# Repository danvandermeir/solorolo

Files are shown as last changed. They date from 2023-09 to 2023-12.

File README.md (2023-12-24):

# SoloRolo
  
This is a FOS(S) set of code and CAD files to assist in creating a single hub motor self balancing skateboard. As I said, this is provided for free. I take no responsibility for whatever may happen with creation of devices from these files. You are (at) your own risk. It is 3D printed, so how strong it is can depend heavily on what you print it with.  
  
That being said, riding around on this thing has been amazing and it has been a great time putting it together. Thanks for the interest. :)  
  
TL;DR for `original` SoloRolo:  
1. choose a battery size using notes at the bottom of this README  
2. choose if you want nice LED headlights (does not effect battery life worth talking about)
3. choose if you want underglow (RGB, can chase ground with rainbow)
4. choose LED strip types (individually addressable [RGB], RGB "analog")
5. download+print [these](mechanical/plastics/)  
6. order [these](BOMs/original/)  
7. check+cut [these](mechanical/metals/original/)  
8. assemble *everything* using [this](electrical/original/) and [this](finished/original/)  
9. program [ESC](code/ESCs/original/) and [Arduino](code/controllers/original/)  
10. button up and roll  
  
**In specific my recommend for creation of a SoloRolo is loosely this order, and it should be inferred that if a named collection does not have an entry in any subsection that `orignal` is to be used:**
1. Take note of the structure of files here so you know you're getting everything you need. It's actually easier done than said.
2. Read about and print/PIM/order [plastics](mechanical/plastics/) as they will take a "long time" to print, even if ordering from a 3D print or PIM company. This is the choice likely to have the most effect on look/feel and other part requirements. Start printing the electronics plate first if you have to make a choice, followed by the resistive footpad.
3. Start putting together and making orders for your parts based on the [original BOM](BOMs/original/). Preferably starting with your frame material from the next step so you can deliberate on certain details without delaying your whole project. If there are different requirements for your named collection they'll be found in [BOMs](BOMs/).
4. Start assembling your electronics. Take your time, and do a good job.
5. Read about and order/cut your [metals](mechanical/metals/). Check for a subsection for your chosen named collection (or use `original`), and start cutting.
6. Now that you have a metal frame to more reasonably mount and attach the hub motor and ESC parts to read about and program your [ESC](electronics/ESCs/). These can be expensive and should be the first thing to verify. Any differing files from the VESC based FESC will be under it's respective subsection.
7. LEDs! And... everything else. You'll need to wait for your electronics plate print. Run all your wires through your frames, stick all your LEDs on the frame that are going there, and mount your electronics to your electronics plate. This will allow easier access to everything as it's all coming together now! :D Absolutely consult the [electronics schematic](electronics/) for your named collection (or `original`).
8. Program your Arduino, lighting controller, or whatever your named collection specifies and test the lights. Usually you can test by mounting your frame to a milk carton and tilting it while applying pressure to to the resistive sensors to verify proper power connections, communication between the lighting controller and the ESC, and proper power and/or data between the lighting controller and the LEDs and or strips.
9. When all your prints are in, assemble all the things! Fasten your cavities to your frame after fishing your wires through during assembly, install all your external interfaces (charge inlet, power button, LEDs and/or strips, screens, readouts, etc), connect all the loose power and data wires according to the [electronics schematic](electronics/) for your named collection (or `original`), fasten your footpads to your cavities, and install any caps or friction coatings (skateboard tape).
10. Test all your functions using your milk crate mount or whatever you've devised, and take 'er out on a catious maiden voyage! Roll! You're probably done! :D  

## The `solorolo_` * `_` * `-`* files subsections, and notes:  
***The first wildcard represents the design name of the parts collection.***  
I designed and uploaded `original`. If I don't like a design change to my orignal designs you can make your own (even if you want to start with mine as a base!) and contribute it under new directory names for replacement/required files.

***The second wildcard represents a battery size.***  
While having a large battery can be a benefit there are a few drawbacks such as weight, length, and usable capacity. The `max` size battery is 48 volts with a ? Amp hour (~960 Watt hour) rating yielding loosely 50-60 miles (85-90 kilometers) per full charge.  
- The weight of the `max` size battery SoloRolo is ~37 pounds (~16.75 kilograms). Is it worth lugging this around?  
<sub>It is for me... I live in a relatively remote area, this is great for exploring where I am not likely to use my SoloRolo for bunny hoping between many indoor locations where I may be able to charge.</sub>
  
- With the `max` size battery at maybe 60 miles (90 kilometers) capacity per charge combined with loosely what is considered a reasonable safe top speed of 18 m/h (~30 km/h) you could potentially be riding for 3 hours and 20 minutes! Will you come close to using this capacity?  
<sub>While rolling is an excellent time, that is a decently long duration that you may never approach with chargers at your stops. Again, I live in a relatively remote area.</sub>
  
- The length of the `max` size battery will limit the terrain and/or incline you are trying to travel. Do you have any steep streets you're looking to roll on?  
<sub>For me there are many steep paved and unpaved paths I take, but even so I can often find a another way up/down.</sub>

***The third and final wildcard represents the name of the part in the size and collection.***

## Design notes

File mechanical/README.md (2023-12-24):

These are the CAD files to be used for 3D printing, PIM, and/or cutting/ordering metals.

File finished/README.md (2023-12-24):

A space for named collections to store some finished product photos, partially to help assembly. Probably mostly glamor shots.

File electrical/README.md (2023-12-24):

Named collections of electrical schematics for a SoloRolo.

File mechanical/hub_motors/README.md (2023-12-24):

Creator named collections of hub motors in case `orignal` isn't for you.  
  
Also, really, it is helpful if you model all your parts that you are creating CAD models to interface with.

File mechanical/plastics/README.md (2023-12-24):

Creator named collections of parts files for 3D printing or PIM to be printed/made/ordered.  
  
If printing yourself absolutely consider using stronger, weather resistant, and more heat resistant plastics for this project. PETG can generally withstand higher weights, sudden shock, and is more heat resistant than most PLA. 3D printing plastics can be complex. YMMV Don't strand yourself due to a structural issue on a roll. /helicopterparent  
  
Following [original](original/) settings of footpads/electronics plate @0.1mm height, 10 perimeter layers, and 100% infill the cavities with these settings took loosely 4 and 4.5 days of continous printing. The footpads took 3.5 and 4 days. The electronics plate under a day. Perhaps consider starting your prints first with the electronics plate followed by the resistive footpad.

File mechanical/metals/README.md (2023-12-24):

Creator named models and mechanical drawings of/for the frame of your SoloRolo.

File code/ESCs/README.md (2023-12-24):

These are named collections of configuration files and instructions for use of Electronic Speed Controllers. Such as the VESC based FESC ESCs.

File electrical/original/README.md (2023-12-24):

This is a loose schematic for the current headlight and underglow iteration I have chosen. Prper update coming soon.

Conceptually the schematic isn't terribly complex.
```
Charge Port > Battery
                v
          Anti Spark Switch > VESC > Hub Motor
                v              v v
 v----< Constant Voltage PSU   | >   Resistor Network
 |              v              |            v
 |      Constant Current PSU   |     Pressure Sensitive Resistors
 |              v              v
 |        Transistor Pair   <  Arduino Nano
 |              v              v
 |    "Custom" LED Headlights  v
 |                             v
 >---------------------------->WS2812B LED strips (bumper1, bumper2, ground)
```
Eventually I will add more variants.

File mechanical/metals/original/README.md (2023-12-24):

-o-

These are the original STL and drawing files I created for cutting aluminum extrusion. An enormous amount of care and detail went into these (measure 9 times, cut 2, print 20, or something). Obligitory "please communicate/contibute" if you see valid changes you'd like to make. :)

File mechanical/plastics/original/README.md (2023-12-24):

-o-

These are the original STL files I created for 3D printing. An enormous amount of care and detail went into these (measure 9 times, cut 2, print 20, or something). Obligitory "please communicate/contibute" if you see valid changes you'd like to make. :)
  
There are headlight cavity and headlight electronics plate models for use with the extra LED Cree headlights listed in the `original` BOM. The Cree LED headlights are optional, but IMO worth it.  
  
I tried following design rules that reduce required support material for 3D printing, and incorperating all holes into the plastic where possible. Cutting metal is more difficult than reprinting for iterative design changes.  
  
Absolutely consider using stronger, weather resistant, and more heat resistant plastics for this project. PETG can generally withstand higher weights, sudden shock, and is more heat resistant than most PLA. 3D printing plastics can be complex. YMMV Don't strand yourself due to a structural issue on a roll.  
  
I used an Elegoo Neptune 3 Max in a "weather sealed" closed, Octoprint on a RPi4B, and around 6 1 kilogram spools of 1.75 millimeter Overture transparent PETG. All prints that I performed were printed at 100% infill with 10 top, bottom, and vertical perimeter layers. My first layer was single layer height (0.1/0.3 millimeter), 40 millimeter brims, no skirt, and organic supports at 40 degrees. The footpads and electronics plate were printed at 0.1 millimeter layer height with the rest being printed at 0.3 millimeter layer height. I did have to watch the footpads print pretty closely as I was closer to the ocean at the time and had a lot of issues with blobing.  
  
The cavities with these settings took loosely 4 and 4.5 days of continous printing. The footpads took 3.5 and 4 days. The electronics plate under a day. Perhaps consider starting your prints first with the electronics plate followed by the resistive footpad.

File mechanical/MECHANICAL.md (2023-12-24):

These are the original STL files I created for 3D printing and cutting aluminum extrusion. An enormous amount of care and detail went into these (measure 9 times, cut 2, print 20, or something). Obligitory "please communicate/contibute" if you see valid changes you'd like to make. :)

I tried following design rules that reduce required support material for 3D printing, and incorperating all holes into the plastic where possible. Cutting metal is more difficult than reprinting for iterative design changes.

Absolutely consider using stronger, weather resistant, and more heat resistant plastics for this project. PETG can generally withstand higher weights, sudden shock, and is more heat resistant than most PLA. 3D printing plastics can be complex. YMMV Don't strand yourself due to a structural issue on a roll.

I used an Elegoo Neptune 3 Max in a "weather sealed" closed, Octoprint on a RPi4B, and around 6 1 kilogram spools of 1.75 millimeter Overture transparent PETG. All prints that I performed were printed at 100% infill with 10 top, bottom, and vertical perimeter layers. My first layer was single layer height (0.3 millimeter). The footpads were printed at 0.1 millimeter layer height with the rest being printed at 0.3 millimeter layer height.

The cavities with these settings took loosely 4 and 4.5 days of continous printing. The footpads took 3.5 and 4 days. Perhaps consider starting your prints first?

## The `solorolo_` * `_` * `-`* files subsections, and notes:  
***The first wildcard represents the design name of the parts collection.***  
I designed and uploaded `original`. If I don't like a design change to my orignal designs you can make your own (even if you want to start with mine as a base!) and contribute it here under a new directory.

***The second wildcard represents a battery size.***  
While having a large battery can be a benefit there are a few drawbacks such as weight, length, and usable capacity. The `max` size battery is 48 volts with a ? Amp hour (~960 Watt hour) rating yielding loosely 50-60 miles (85-90 kilometers) per full charge.  
- The weight of the `max` size battery SoloRolo is ~37 pounds (~16.75 kilograms). Is it worth lugging this around?  
<sub>It is for me... I live in a relatively remote area, this is great for exploring where I am not likely to use my SoloRolo for bunny hoping between many indoor locations where I may be able to charge.</sub>
  
- With the `max` size battery at maybe 60 miles (90 kilometers) capacity per charge combined with loosely what is considered a reasonable safe top speed of 18 m/h (~30km/h) you could potentially be riding for 3 hours and 20 minutes! Will you come close to using this capacity?  
<sub>While rolling is an excellent time, that is a decently long duration that you may never approach with chargers at your stops. Again, I live in a relatively remote area.</sub>
  
- The length of the `max` size battery will limit the terrain and/or incline you are trying to travel. Do you have any steep streets you're looking to roll on?  
<sub>For me there are many steep paved and unpaved paths I take, but even so I can often find a another way up.</sub>

***The third and final wildcard represents the name of the part in the size and collection.***

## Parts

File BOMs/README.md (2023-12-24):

Collection of Bill Of Materials to be used with named collections of SoloRolo PEVs.

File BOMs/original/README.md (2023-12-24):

This is a loose parts list with prices and ordering locations to create the `original` SoloRolo.

HUB                    $1                    https://example.tld

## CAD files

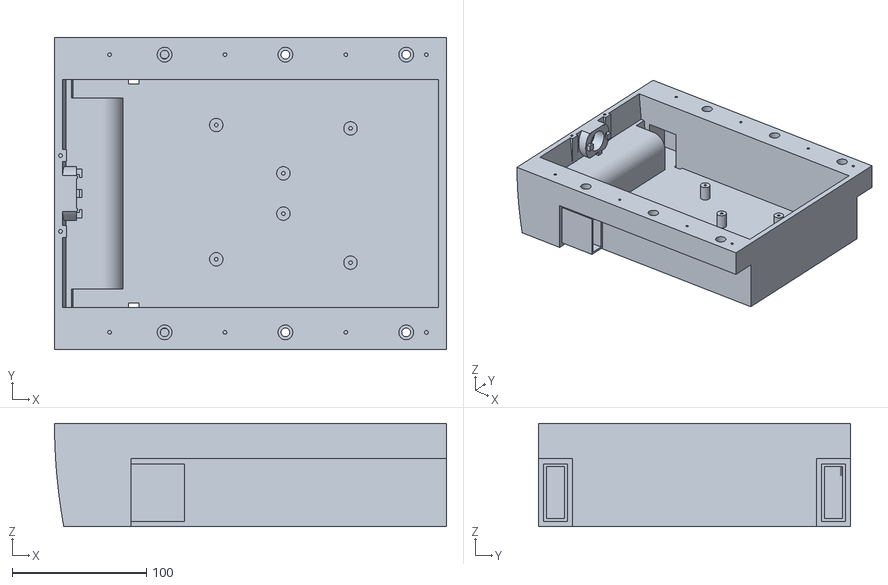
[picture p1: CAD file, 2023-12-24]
mechanical/plastics/original/solorolo_original_max-electronics_cavity_headlight.stl
292.0 x 232.3 x 77.0

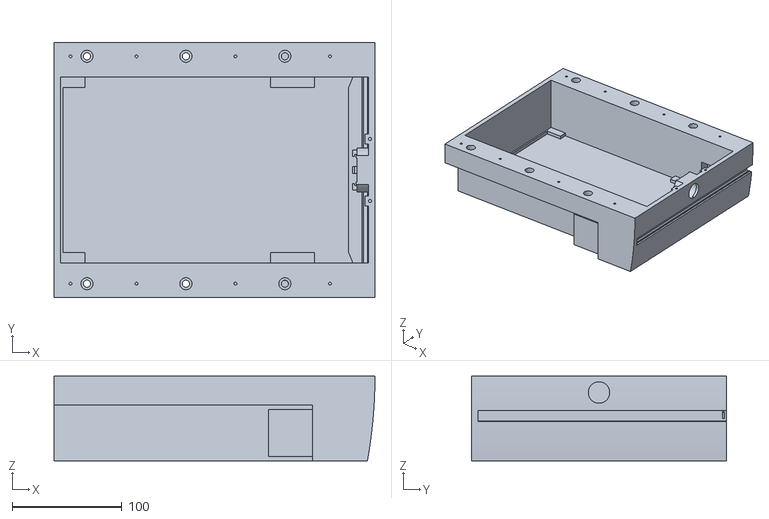
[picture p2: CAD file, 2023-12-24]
mechanical/plastics/original/solorolo_original_max-battery_cavity_headlight.stl
292.0 x 232.3 x 77.0

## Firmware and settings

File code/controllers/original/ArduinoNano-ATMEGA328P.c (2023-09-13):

void timer(){
  if(/*timer is fresh*/){
    //turn data pins high
    //set timmer interrupt time for .4us
    if(cereal=0){
      //turn data pins low
      //set timer interrupt time for 301us
    }
    if(cerealcount=cereal)
      cereal = 0;
    else
      ++cereal;
  }elif(/*timer is .4us*/){
    //datapins = supercereal[cereal];
    //set timer interrupt time for .8us
  }elif(/*timer is .8us*/){
    //turn data pins low
    //set
  }elif(/*timer is 301us*/)
    //set timer count to nearly expire
}

void SPIcomms(){
  switch(SPIstatus)
  {
    case 1:
      //start SPI read
      SPDR = 0xFF;
      SPIstatus = 2;
      break;
    case 2:
      //start SPI read
      SPIstatus = 3;
      break;
    case 3:
      //start SPI read
      SPIstatus = 4;
      break;
    case 4:
      //start SPI read
      SPIstatus = 5;
      break;
    case 5:
      //start SPI read
      SPIstatus = 6;
      break;
    case 6:
      //start SPI read
      SPIstatus = 255;
      break;
    case default:
      if(){//read if timer for ~120Hz has reached max to begin reading VESC through SPI
        SPIstatus = 1;
        //reset timer counter
      }
      break;
}

void HSVtoRGB(){
    if(Value==0)
        RedBrightness = GreenBrightness = BlueBrightness = 0;
    else{
        uint16_t tmp16;
        uint8_t HueDivCount,Y,Z;
        //solve for Y, Y = (Value*(255-Saturation))/255;
        Y = 255-Saturation;
        tmp16 = Value*Y;//top is 65025
        while(tmp16>254){//divide by 255
            tmp16 -= 255;
            ++Y;
        }
        if(tmp16>127)//round the remainder
            ++Y;
        //solve to get appropriate action for HSV to RGB, Hue/6
        tmp16 = Hue;
        HueDivCount = 0;
        while(tmp16>10922){
            tmp16 -= 10923;//if HueDivCount=5 top is 10920 (2/65535)0.00003051%/(2/10922)0.0001831% deviation from real due to integer only math
            ++HueDivCount;
        }
        if(HueDivCount==5)//offset number so maximum value stays true
            tmp16 += 2;
        //solve for Z, Z = (Value*(Saturation*HueRemain))/2785110, if HueDivCount=1,3,5 then invert the value
        Z = 0;
        while(tmp16>42){//divide to 8 bit size so next operation does not exceed 16 bit size
            tmp16 -= 43;
            ++Z;
        }
        if(tmp16>21)//round the remainder
            ++Z;
        tmp16 = Z*Saturation;
        Z = 0;
        while(tmp16>253){//divide to 8 bit size so next operation does not exceed 16 bit size
            tmp16 -= 254;
            ++Z;
        }
        if(tmp16>126)//round the remainder
            ++Z;
        tmp16 = Z*Value;
        while(tmp16>254){//divide to 8 bit size so next operation does not exceed 16 bit size
            tmp16 -= 255;
            ++Z;
        }
        if(tmp16>127)//round the remainder
            ++Z;
        switch(HueDivCount){
            case 0:
                RedBrightness = Value;
                GreenBrightness = Z;
                BlueBrightness = Y;
                break;
            case 1:
                RedBrightness = 255-Z;
                GreenBrightness = Value;
                BlueBrightness = Y;
                break;
            case 2:
                RedBrightness = Y;
                GreenBrightness = Value;
                BlueBrightness = Z;
                break;
            case 3:
                RedBrightness = Y;
                GreenBrightness = 255-Z;
                BlueBrightness = Value;
                break;
            case 4:
                RedBrightness = Z;
                GreenBrightness = Y;
                BlueBrightness = Value;
                break;
            case 5:
                RedBrightness = Value;
                GreenBrightness = Y;
                BlueBrightness = 255-Z;
                break;
        }
    }
}




bool digitalLED = true;
bool stripheadlight = false;
uint_16t PEVmaxmmpersecond = 20000;
uint_16t HSVmaxmmpersecondtohuerotation = 6000;
uint_16t HSVminmmpersecondtohuerotation = 500;
if(digitalLED){
  uint_16t LEDpixelcount = 46;
  uint_16t LEDcountpermeter = 60;
}





bool forwardtravel = usefirstLEDbuffer = true;
bool SPIdataready = braking = LEDupdaterequest = firstLEDbufferready = secondLEDbufferready = false;
uint_8t x = SPIstatus = Saturation = Value = 255;
uint_16t y = Hue = MMpersecond = pixelpositionstart = 0;
uint_32t z = uMperLEDrefreshbuffer = uMperLEDrefresh = 0;
uint_16t totalLEDs = 3 * LEDpixelcount;
uint_16t HSVpixelpixeldistanceuM = 1000000 / ( LEDcountpermeter + 1 );//adjust for dead space on both ends of the led strip
uint_16t HSVmaxprepixelcount = HSVmaxmmpersecondtohuerotation / HSVpixelpixeldistanceuM;
uint_16t HSVprehuestep = 65535 / ( HSVmaxprepixelcount + 1 );//adjust so end!=begin number, minor resolution lost
uint_8t Gprecalculated[HSVmaxprepixelcount] = {0};
uint_8t Rprecalculated[HSVmaxprepixelcount] = {0};
uint_8t Bprecalculated[HSVmaxprepixelcount] = {0};
uint_8t firstLEDbuffer[totalLEDs] = {0};
uint_8t secondLEDbuffer[totalLEDs] = {0};
for (i=0; i<=HSVmaxprepixelcount; ++i){
    HSVtoRGB();
    Gprecalculated[i] = GreenBrightness;
    Rprecalculated[i] = RedBrightness;
    Bprecalculated[i] = BlueBrightness;
    Hue += HSVprehuestep;
}
if(digitalLED){
  uint_16t HSVpixelskip = 1;
  uint_16t HSVpixelskipmin = HSVmaxprepixelcount / ( HSVminmmpersecondtohuerotation / HSVpixelpixeldistanceuM );
}

void main(){
  SPIcomms();
  if(SPIstatus==255){//if SPI communication completed
    uMperLEDrefresh = ;//convert data from SPI communication to micrometer per polling cycle, milimeter per second, and direction
    z = ( uMperLEDrefresh * 120 );
    MMpersecond = ( z / 1000 );
    forwardtravel = ;


    while(uMperLEDrefresh>=HSVpixelpixeldistanceuM){//calculate distance traveled to determine new starting pixel
      ++pixelpositionstart;
      if(pixelpositionstart>HSVmaxprepixelcount)
        pixelpositionstart = 0;
      uMperLEDrefresh -= HSVpixelpixeldistanceuM;
    }
    uMperLEDrefreshbuffer += uMperLEDrefresh;
    if(uMperLEDrefreshbuffer>=HSVpixelpixeldistanceuM){
      ++pixelpositionstart;
      if(pixelpositionstart>HSVmaxprepixelcount)
        pixelpositionstart = 0;
      uMperLEDrefreshbuffer -= HSVpixelpixeldistanceuM;
    }


    if(digitalLED){
      if(MMpersecond>=HSVmaxmmpersecondtohuerotation)//calculate precalculated pixel colors to be skipped based on speed
        HSVpixelskip = 1;
      elif(MMpersecond<=HSVminmmpersecondtohuerotation)
        HSVpixelskip = HSVpixelskipmin;
      else
        HSVpixelskip = HSVmaxprepixelcount / ( HSVmaxmmpersecondtohuerotation / HSVpixelpixeldistanceuM );
    }

    SPIdataready = true;
    LEDupdaterequest = true;
  }
  if(LEDupdaterequest){
    if(digitalLED){
      //update headlight
      //update brakelight
      if(SPIdataready){
        if(braking){//update brakelights
          if(forwardtravel)
            bumper2 = 0x00FF00;
          else
            bumper1 = 0x00FF00;
        }else{
          if(forwardtravel)
            bumper2 = 0x000000;
          else
            bumper1 = 0x000000;
        }
        if(stripheadlight){//update headlights
          if(forwardtravel)
            bumper1 = 0xFFFFFF;
          else
            bumper2 = 0xFFFFFF;
        }else{
          if(forwardtravel){
            bumper1 = 0x000000;
            //turn bumper1 headlight pin on
            //turn bumper2 headlight pin off
          }else{
            bumper2 = 0x000000;
            //turn bumper1 headlight pin off
            //turn bumper2 headlight pin on
          }
        }
        y = pixelpositionstart;
        if(usefirstLEDbuffer){
          for (uint_8t i=0; i<=totalLEDs; ++i){
            secondLEDbuffer[i] = Gprecalculated[y];
            ++i;
            secondLEDbuffer[i] = Rprecalculated[y];
            ++i;
            secondLEDbuffer[i] = Bprecalculated[y];
            y += HSVpixelskip;
          }
          secondLEDbufferready = true;
        }else{
          for (uint_8t i=0; i<=totalLEDs; ++i){
            firstLEDbuffer[i] = Gprecalculated[y];
            ++i;
            firstLEDbuffer[i] = Rprecalculated[y];
            ++i;
            firstLEDbuffer[i] = Bprecalculated[y];
            y += HSVpixelskip;
          }
          firstLEDbufferready = true;
        }
      }else{
        if(usefirstLEDbuffer)
          secondLEDbufferready = true;
        else
          firstLEDbufferready = true;
      }
    }else{
      if(braking){
        if(forwardtravel){//update brakelights
          //turn R pins on on bumper2
          //turn GB pins off on bumper2
        }else{
          //turn R pins on on bumper1
          //turn GB pins off on bumper1
        }
      }else{
        if(forwardtravel){
          //turn RGB pins off on bumper2
        }else{
          //turn RGB pins off on bumper1
        }
      }
      if(stripheadlight){//update headlights
        if(forwardtravel)
          //turn RGB pins on on bumper1
        else
          //turn RGB pins on on bumper2
      }else{
        if(forwardtravel){
          //turn RGB pins off on bumper1
          //turn bumper1 headlight pin on
          //turn bumper2 headlight pin off
        }else{
          //turn RGB pins off on bumper2
          //turn bumper1 headlight pin off
          //turn bumper2 headlight pin on
        }
      }
    }
  }
}

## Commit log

2023-09-13 Create ArduinoNano-ATMEGA328P.c
    First commit, unfinished
2023-12-24 Update and rename solorolo_original_max-battery_cavity.stl to solorolo_original_max-battery_cavity_headlight.stl
    [solorolo_original_max-battery_cavity_headlight.stl]
